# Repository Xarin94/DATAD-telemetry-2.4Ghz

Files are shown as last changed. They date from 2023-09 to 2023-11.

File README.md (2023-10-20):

# DATAD telmetry board 2.4GHz

This is the basic firmware of a teensy 4.0 to achieve a full duplex, programmable solution for a fast and long range datalink.

The goal is to achive a flexible platform for makers with little knowledge in programming, of a fleixible and reliable radio link.
[Arduplane Forum](https://discuss.ardupilot.org/t/datad-2-4ghz-telemetry-link-2-w-open-source/104818)

## Features

- SX1280 based, on 2.4GHz small directional antennas can extend the range easily.
- Various I/O: usb serial, 4 serial (3 PWM capable), canbus, and I2C.
- Mavlink indipendent, created for the use on UAV's, but adaptable to every UART device. (transparent link, valid also for CANBUS)
- Indipendent RX and TX antennas, for optimal antenna placement.
- Full duplex: one sx1280 amplified at 2w maximum and one specific for reception.
- One sx1280 can be used for RX, TX and ranging.
- High speed and long ange FLRC modulation, or LoRa comminication selectable.
- Added the possibilty to read a PPM from a RC controller and inject in the autopilot via Mavlink messages.

## Usage
To avoid any damage on the reciving end, when using high power output DO NOT point antennas direcly to each other! SX1280 maximum input power is 6dB not 34!
In future we will implement a power output dependent on the RSSI from the other radio, but the risk of burning the reciving end remains.
An heat sink is suggested for continous trasmission, for example with a arduplane 50Hz telemetry on SR0 and EXTRA1, the remining at 10hz, no heatsink is needed.

### antennas and power

To correcly install the antennas on the drone keep in mind:
 - distance between the antennas is a must, higher is better.
 - you can use one vertically placed and one horizontally, different polarization will help with a loss of around 10dB.
 - my best choiche for mounting antennas is one on top of the other, with a 5dBi antnnenas the connector part is in a "shadow zone".
 - you can use RP-SMA cables to place the antennas where you want.
 - to power the board use a spare jst gh 4 pin connector to provide 5v to the board (in the old version do not use the 6-26v port, it will overheat and power off).

## Programming the Teensy 4.0

To program the main board you can use Arduino IDE with the needed libraries
The program in the same for the air and ground unit, with the paramenters you can select all the neededfunction of the radio.

The options are:
 - RadioType: 0 to select ground unit, 1 to select air unit. With this selection the rx and tx frequencies are automatically swapped and the RC in/out is automatically selected to have PPM in on the ground and PPM out on the air unit.
 - Rxfreq: the Reciving frequency of the ground unit and trasmitting on the air unit.
 - Txfreq: the opposite.
 - SPD: you can chose between 325,650,1300, those are MBPS, the best compromise is with a Correction of 3/4 for all the speeds, so the effective datarate is 25% than indicate. You can modify the correction param in the SX1280 initialization.
 - TxPower: The output power is accettable between 0 and -18dB from the sx1280, more than zero can damage the amplifier. The output is proportional the the input before the amplifer, at -18 the output is 20dB, at maximum 34,5db at 0 selected.
 - TelemID: unique code for the link, if multiple radios are on the same frequency you can use this paramenter so separate the messages, or to direct the messages to moltiple ports.
 - RCbusID: unique id to the PPM trasmission, same for the TelemID.
 - RCbusrate: delay in milliseconds between ppm packets, with two separate channels you can send lots of data without inferering with the telemetry downlink.
 - RCbuschannels: selectable number of channels needed, normally 16, encodable in the mavlink message only 8.
 - RCbuspin: the input/output pin of the PPM same on the air and ground unit normally, but you can customize it(check the exposed Serial ports, Serial3 is capable of high speed ppm).
 - RCouttype: 2 for PPM on the selected pin, 1 for the mavlink mix in the telemetry link ( SERVO_OVERRIDE function, like mission planner does).

After selecting all the prams you need to change from Serial to Serial1 functions between air and ground unit, depending on witch port you want to use.
There modification in needed in the first part of the program, in the reading part: the main function is Serial.available(), the second one and third are Serial.read().
the output is done on Serial and Serial1 at the same time.

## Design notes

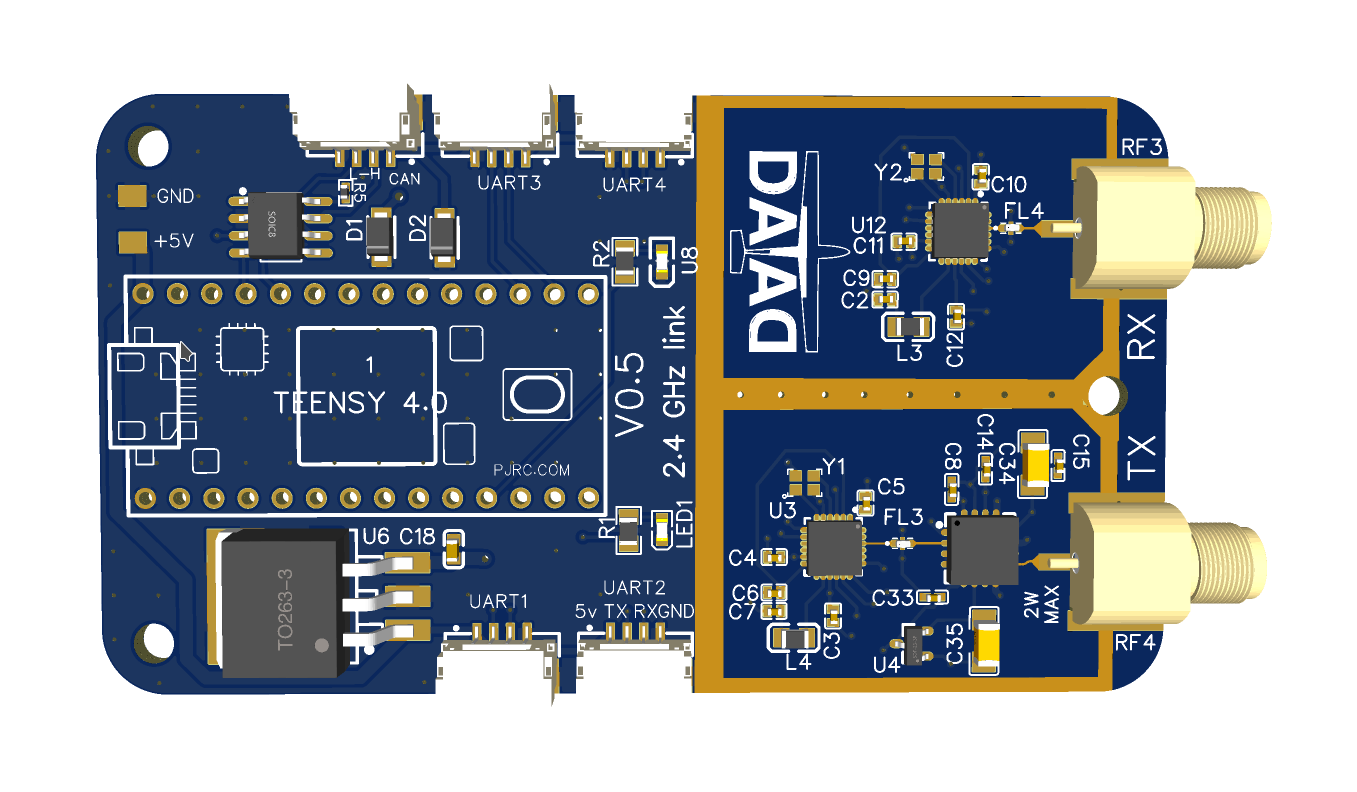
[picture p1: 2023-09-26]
Screenshot_20230926_120951.png

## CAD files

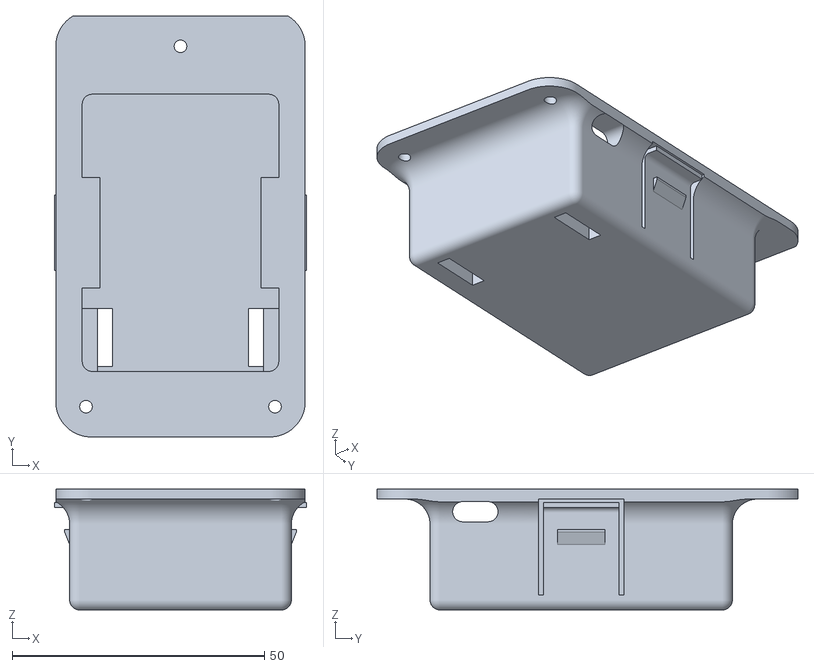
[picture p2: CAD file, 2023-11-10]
Case/JR bay adapter (not tested).stl
50.0 x 83.5 x 24.0

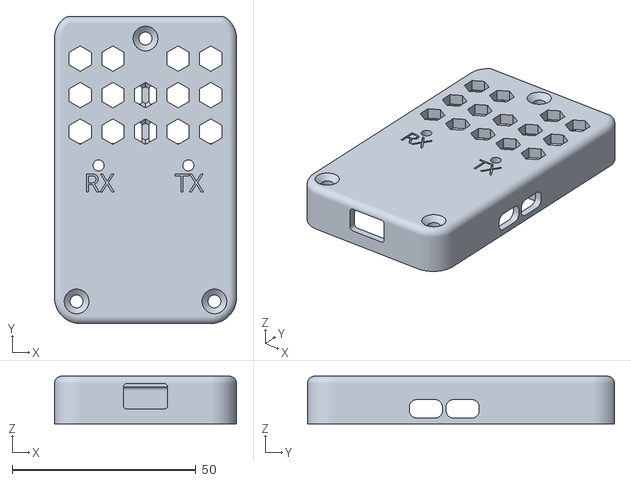
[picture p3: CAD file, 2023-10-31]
Case/top cover vented (suggested).stl
49.5 x 83.5 x 13.0

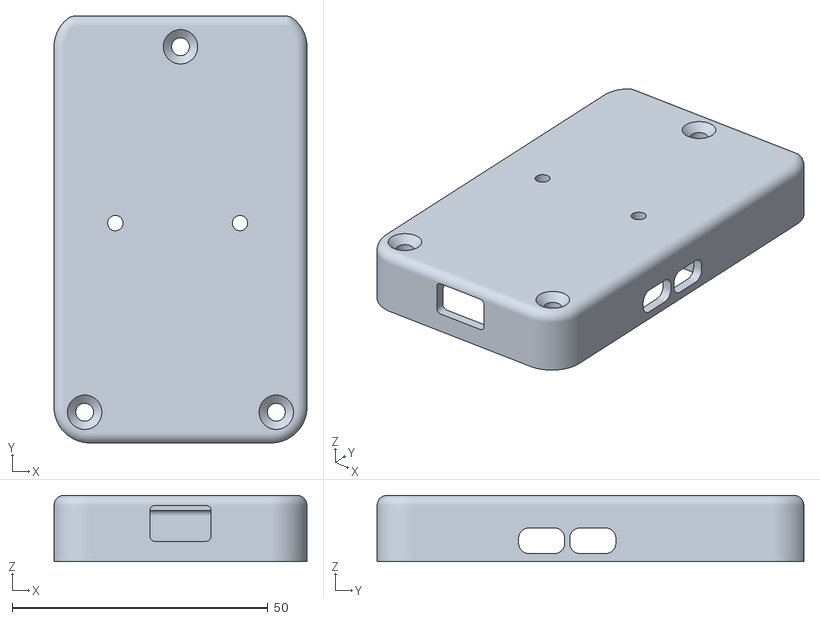
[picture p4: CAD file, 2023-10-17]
Case/top cover.stl
49.5 x 83.5 x 13.0

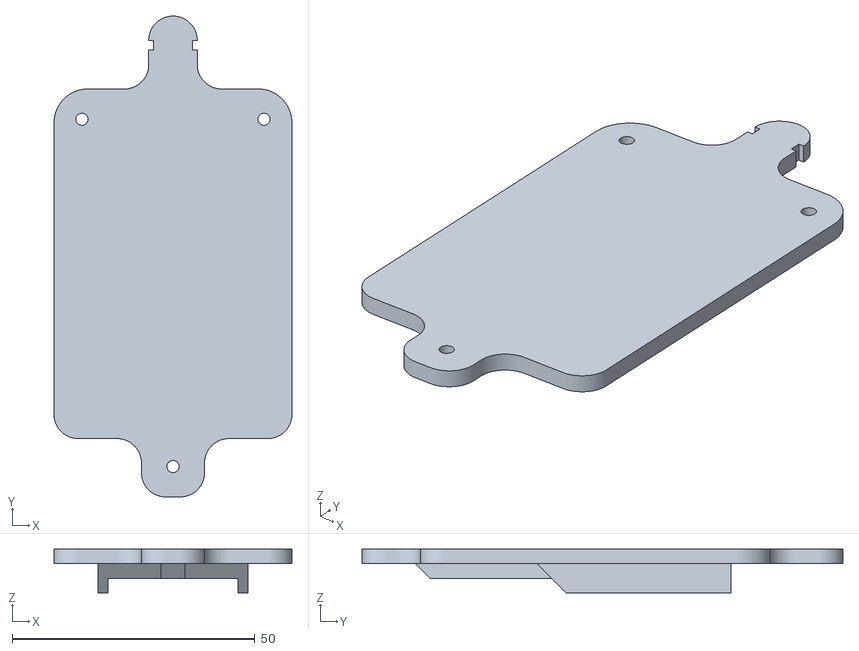
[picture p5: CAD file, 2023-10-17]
Case/nano bay attach.stl
49.0 x 99.0 x 9.00

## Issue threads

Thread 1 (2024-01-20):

Teensy module restarts while connecting

karthikgn, 2024-01-20:
Hi.,

I tried using your code, Teensy board restart while connecting to the mission planner. when this will happen is huge data transmit and receive at that that time air or ground module will restart. help us to resolve this.

Thank You.,

Xarin94, 2024-01-20:
This is strange, teensy should not reboot during connection, Mission plannes should read and write to the com port, is the wiring all checked? seems a power drop

karthikgn, 2024-01-23:
thank you.,

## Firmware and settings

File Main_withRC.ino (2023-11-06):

#include <RadioLib.h>
#include <string.h>
#include <PPMReader.h>
#include <mavlink.h>
#include <PulsePositionIMXRT.h>

//////////////pinout of the board//////////////
//////////////////DO NOT CHANGE////////////////

#define LEDtx 9
#define LEDrx 2
#define CSS1 3
#define DIO11 6
#define NRST1 4
#define BUSY1 5
#define CSS2 10
#define DIO12 19
#define NRST2 21
#define BUSY2 20
////////////////////////////////////////////////

///////////Radio params/////////////////////////

#define RadioType 0      //1 air 0 gnd
#define Rxfreq 2415      //rx frequncy-> different from tx
#define Txfreq 2475      //select between 2400 and 2480 mhz
#define SPD 650          //speed kbps-> 325 / 650 / 1300
#define TxPower -2      //output power -2 -> 34 dB, -18 ->20 dB  you can set any power in this range (check for legality)
#define TelemID 25       //ID of he messages for the mavlink messages (0-254)
#define RCbusID 12       //-1 if not used (additional id for sbus)
#define RCbusrate 50     //delay in milliseconds for the sbus rate
#define RCbuschannels 8  //numers of ppm channels       mavlink max 8         ppm out max 16
#define RCbuspin 15      //Rx serial 4 pin    pins:   14, 15, 18 capable of ppm out precisely
#define RCoutype 2       //type of PPM output on air unit 1-> mavlink mix  2-> PPPm out on RXbuspin
////////////////////////////////////////////////

PPMReader ppm(RCbuspin, RCbuschannels);
PulsePositionOutput PPMout;

SX1280 radio = new Module(CSS1, DIO11, NRST1, BUSY1);   //tx pin 17
SX1280 radio2 = new Module(CSS2, DIO12, NRST2, BUSY2);  //rx pin 16


int transmissionState = RADIOLIB_ERR_NONE;
int num = 0;
const uint8_t MaxMessageSize = 120;
uint8_t Message[MaxMessageSize];
uint8_t MSG[MaxMessageSize];
int msgrx = 0;
int Rssi = 0;
int recivedBytes = 2;
unsigned long int RCbusTimer = 0;
unsigned long int msgtimeTX = 0;



void setup() {
  RCbusTimer = millis();
  msgtimeTX = micros();
  if (RCoutype == 2 && RadioType == 1) {
    PPMout.begin(RCbuspin);
  }
  SPI.beginTransaction(SPISettings(10000000, MSBFIRST, SPI_MODE0));
  Serial.begin(115200);
  Serial1.begin(115200);  //set if serial output is needed at the gnd station / air port
  pinMode(LEDrx, OUTPUT);
  pinMode(LEDtx, OUTPUT);
  pinMode(RCbuspin, INPUT_PULLDOWN);
  if (RadioType == 0) {
    int state = radio.beginFLRC(Txfreq, SPD, 3, TxPower, 16, 0);
    Serial.println(state);
    state = radio2.beginFLRC(Rxfreq, SPD, 3, TxPower, 16, 0);
    Serial.println(state);
  }
  if (RadioType == 1) {
    int state = radio.beginFLRC(Rxfreq, SPD, 3, TxPower, 16, 0);
    Serial.println(state);
    state = radio2.beginFLRC(Txfreq, SPD, 3, TxPower, 16, 0);
    Serial.println(state);
  }
  uint8_t syncWord[] = { 0x01, 0x23, 0x45, 0x67 };
  radio.setSyncWord(syncWord, 4);
  radio2.setSyncWord(syncWord, 4);
  radio.setDio1Action(setFlagTX);
  radio2.setDio1Action(setFlagRX);
  radio2.setHighSensitivityMode(true);
  radio2.startReceive();
}

volatile bool transmittedFlag = true;
volatile bool receivedFlag = false;

void setFlagTX(void) {

  transmittedFlag = true;
}

void setFlagRX(void) {
  // we got a packet, set the flag
  receivedFlag = true;
}

void loop() {
  while (Serial.available() > 0 && recivedBytes <= MaxMessageSize) {  //change Serial with Serial1 for the air, and vice versa
    if (recivedBytes == 2) {
      Message[0] = TelemID;
      Message[1] = 0;
    }
    Message[recivedBytes] = Serial.read();  //change Serial with Serial1 for the air, and vice versa
    recivedBytes++;
    msgtimeTX = micros();
  }

  if (Serial.available() == 0 && micros() - msgtimeTX > 5000 && recivedBytes > 2) {  //change Serial with Serial1 for the air, and vice versa (this function sends incomplete messages after 50millis, for higherd bauds lower it)
    for (int i = recivedBytes; i < MaxMessageSize; i++) {
      Message[i] = '\0';
    }
    recivedBytes = MaxMessageSize;
    msgtimeTX = micros();
  }

  if (millis() - RCbusTimer > RCbusrate && recivedBytes == 2 && RadioType == 0 && RCbusID != -1 && ppm.latestValidChannelValue(1, 0) != 0) {
    Message[0] = 254;  //specific for sbus messsage
    Message[1] = RCbusID;
    for (int i = 0; i < RCbuschannels * 2; i = i + 2) {
      Message[i + 2] = ppm.latestValidChannelValue((i + 2) / 2, 0) & 0xff;
      Message[i + 3] = (ppm.latestValidChannelValue((i + 2) / 2, 0) >> 8);
    }
    RCbusTimer = millis();
    recivedBytes = MaxMessageSize;
  }



  if (transmittedFlag == true && recivedBytes >= MaxMessageSize) {  //TX when message full and flag permits
    digitalWrite(LEDtx, HIGH);
    recivedBytes = 2;
    transmittedFlag = false;
    radio.transmit(Message, MaxMessageSize);
    //radio.finishTransmit()#include <PulsePositionIMXRT.h>;
    digitalWrite(LEDtx, LOW);
  }


  if (receivedFlag) {  //RX packet ready to serialize every time is recived something
    // reset flag
    receivedFlag = false;
    digitalWrite(LEDrx, HIGH);
    int state2 = radio2.readData(MSG, MaxMessageSize);
    //Serial.println(radio2.getRSSI());
    Rssi = map(radio2.getRSSI(), -106, 0, 0, 254);  //get an rssi to build mavlink radio message,future implementation
    if (MSG[0] == TelemID) {
      for (int i = 2; i < MaxMessageSize; i++) {
        Serial.print(char(MSG[i]));
        Serial1.print(char(MSG[i]));  //mirror msg to ext port
      }
    }
    if (MSG[0] == 254 && MSG[1] == RCbusID && RadioType == 1 && RCbusID != -1 && RCoutype == 1) {
      //syntetize PPM  in a mavlink message

      mavlink_message_t message;

      uint8_t target_system = 1;
      uint8_t target_component = 1;
      uint16_t ch1 = (MSG[3] << 8) | MSG[2];
      uint16_t ch2 = (MSG[5] << 8) | MSG[4];
      uint16_t ch3 = (MSG[7] << 8) | MSG[6];
      uint16_t ch4 = (MSG[9] << 8) | MSG[8];
      uint16_t ch5 = (MSG[11] << 8) | MSG[10];
      uint16_t ch6 = (MSG[13] << 8) | MSG[12];
      uint16_t ch7 = (MSG[15] << 8) | MSG[14];
      uint16_t ch8 = (MSG[17] << 8) | MSG[16];
      uint8_t buf[MAVLINK_MAX_PACKET_LEN];
      mavlink_msg_rc_channels_override_pack(255, 254, &message, target_system, target_component, ch1, ch2, ch3, ch4, ch5, ch6, ch7, ch8);
      uint16_t len = mavlink_msg_to_send_buffer(buf, &message);
      Serial1.write(buf, len);
    }
    if (MSG[0] == 254 && MSG[1] == RCbusID && RadioType == 1 && RCbusID != -1 && RCoutype == 2) {
      //ppm synt
      for (int i = 0; i < RCbuschannels; i++) {
        PPMout.write(i + 1, ((MSG[i*2 + 3] << 8) | MSG[i*2 + 2]));
      }
    }
    radio2.startReceive();  //starat reciving new msg
    digitalWrite(LEDrx, LOW);
  }
}

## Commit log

2023-10-13 Update Main_RcPPM.ino
    minor bugs
    [Main_RcPPM.ino]
2023-10-17 added cover top and nano bay adapter
    [nano bay attach.stl, top cover.stl]
2023-11-06 Update and rename Main_RcPPM.ino to Main_withRC.ino
    fixed PPM synt
    [Main_withRC.ino]
